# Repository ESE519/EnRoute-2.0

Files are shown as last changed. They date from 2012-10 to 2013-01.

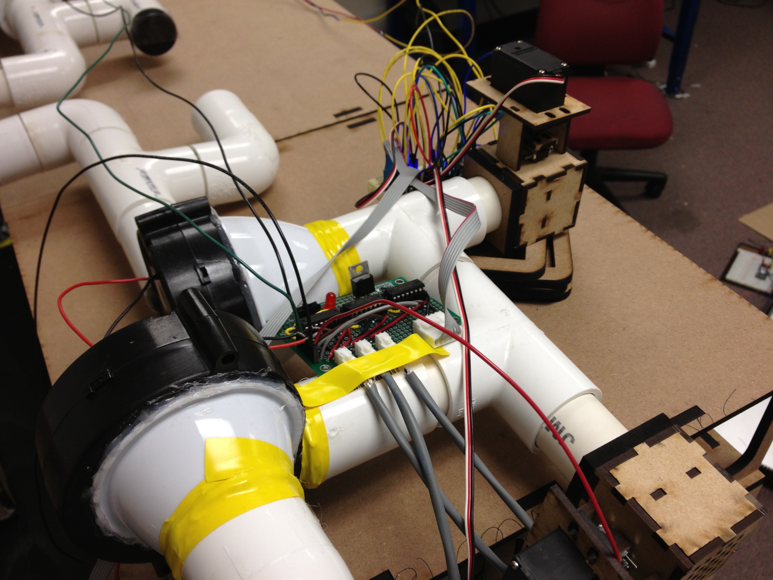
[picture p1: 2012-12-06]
PhotoShoot/Pics_11_30/Photo Nov 28, 2 21 02 PM.jpg

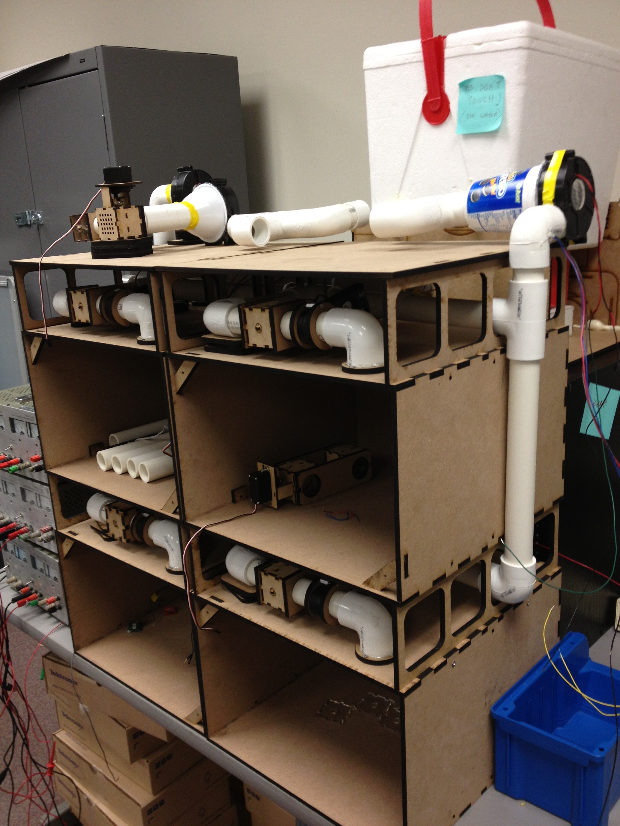
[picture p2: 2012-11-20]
PhotoShoot/Pics_11_19/Photo Nov 19, 3 16 37 PM.jpg

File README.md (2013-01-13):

EnRoute-2.0
===========

This is team 01's final project for Real Time and Embedded Systems course (ESE 519), fall 2012. 
The project is version 2.0 of EnRoute 1.0, an intelligent HVAC testbed.

Team Members:
1) Shah, Neel S.      : shahneel@seas.upenn.edu
2) Vadakedathu, Larry : vlarry@seas.upenn.edu
3) Wheeler, Dan       : dwheeler@seas.upenn.edu

Thank you!

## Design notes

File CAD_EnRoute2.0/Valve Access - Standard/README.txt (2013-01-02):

Valve Access:
These small pieces forms the link with the servo with the help of a 2*4-40 1/2" bolts and corresponding nuts & washers.
This is applicable to any type of valve in this testbed.

EnRoute2.0

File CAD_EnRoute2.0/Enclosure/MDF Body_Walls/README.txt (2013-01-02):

1) Due to the sheer dimensions of the walls, they were not laser cut but measured and cut using a power saw. 
2) The design is such that the front cover can be completely taken out but unscrewing from the L-brackets.
3) These L-brackets are screwed in with our custom designed nut-lock.

EnRoute2.0

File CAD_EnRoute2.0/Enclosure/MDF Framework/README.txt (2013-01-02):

Enclosure Front:
1) In red, the MDF pieces that form the framework including the handles and connecting pieces.
2) In white, how the complete front looks. The center window is 2*(32X16) clear acrylic sheets.

EnRoute2.0

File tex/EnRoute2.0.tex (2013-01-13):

\documentclass[a4paper,10pt,twocolumn]{article}
\usepackage{fullpage}
\usepackage{hyperref}
\usepackage{epsfig}
\usepackage{graphicx}
\usepackage{caption}
\usepackage{subcaption}

\usepackage{stfloats}

\begin{document}

\title{{\bf EnRoute 2.0 - The HVAC Test-Bed} \\ \normalsize\url{https://github.com/ESE519/EnRoute-2.0/wiki/_pages}}
\date{December 15, 2012}
\author{Dan Wheeler \\dwheeler@seas.upenn.edu
        \and Larry Vadakedathu \\vlarry@seas.upenn.edu
	\and Neel D Shah \\shahneel@seas.upenn.edu}
\maketitle

\begin{figure}[ht]
\centering
\epsfig{file=enroute2.eps,width=\linewidth,clip=}
\caption{EnRoute2.0 Complete Assembly}
\label{enroute2}
\end{figure}

\vspace{-5 mm}

\begin{center}
{\bf Introduction}
\end{center}

EnRoute 2.0, as seen in \ref{enroute2}, is an expansion project based on previous work--EnRoute:  The Energy Router Test-Bed--which was aimed at creating a building simulation test-bed for the testing of control algorithms with the goal of improvements in energy scheduling and peak power reduction.  EnRoute 2.0 hopes to expand on the original project through two major components:  creating a more realistic test-bed more closely related to real world HVAC systems, and allowing anyone to run simulations on the test-bed remotely.  The first task is achieved largely through the introduction of ductwork with Variable Air Volume (VAV) control to each room handled through small servo valves and an Air Handling Unit (AHU) distributing air, reclaiming air, and recycling air.  Remote operation is achieved with IP communication using a static IP address supplied specifically for the master mBed controller of the system.

For large scale buildings, electricity costs vary with time based on total demand of the aggregate of consumers.  In such a scenario, energy can cost up to 200 times as much during peak operating hours as it does during normal operating conditions, or during the night when energy is at its cheapest due to low overall demand.  Additionally, peaks in power consumption of an individual facility can result in costly fines.  Therefore, if you can schedule your energy use efficiently to (1) avoid peaks in individual power, and (2) minimize the total power consumption during peak operating hours you could significantly reduce the total cost of electricity incurred.

Unfortunately, current systems are not designed to provide this type of operation.  Firstly, control units have no knowledge of how electricity costs are changing with time, and secondly, units operate almost entirely independent of each other.  We can view the second scenario in the case of cooling two rooms.  Initially one room is cooling while the other room is within its bounds for temperature control, therefore the system is only using approximately half its total power.  If the second room reaches its high threshold point it will switch on and both rooms will begin to cool.  If systems had an overall notion of what other nodes were doing it would be able to schedule the energy use so that all rooms stay within specified bounds, but also ensure that the system is not operating at maximum power if it does not need to be.

\begin{center}
{\bf Project Goals}
\end{center}

The first EnRoute project utilized four (4) mutually exclusive zones which were heated using incandescent lightbulbs with operation points at 0\%, 25\%, 50\%, 75\%, and 100\% of total power.  Cooling was not successfully implemented here, rather it was simulated by heating up the rooms and 'cooling' them by exhausting the warm air to the outside.  While algorithms were effectively developed on this system it lacked reality when compared to real-world buildings which most often achieve heating and cooling through HVAC units which deliver temperature controlled air from the unit itself to multiple rooms.  To improve the realistic aspects of this project we set out to design a system which mimicked an actual HVAC system as best we could as well as to provide methods for cooling.

\begin{figure}[t]
\centering
\epsfig{file=front.eps,width=0.8\linewidth,clip=}
\caption{View of All Zones}
\label{front}
\end{figure}

Firstly, an understanding of HVAC systems is critical to grasp what we wanted to achieve with this test-bed.  At the heart of every HVAC system is the Air Handler Unit (AHU) which has three main functions:  supply air to the ductwork using a blower, pull air from the rooms using a second blower, and allow for the ability to recycle air back into the HVAC.  Next most important are the cooling and heating coils, which are frequently (depending on the size of the system) located coaxially in the HVAC unit so that air is pulled over both coils in series.  A third important feature, which becomes critical for peak energy reduction, is the Variable Air Volume (VAV) control of the system which changes the amount of air pumped into the ductwork based on how much flow each room is requesting.  Our design seeks to meet all three of the goals with the implementation of an AHU, both heating and cooling elements, and VAV control.

The next goal of this project was aimed not only at creating a test-bed, but an open-source test-bed which could be used by anyone (assuming permission is given) to run their own simulations remotely (i.e. from anywhere in the world).  

\begin{center}
{\bf Hardware:  Structural Design and Implementation}
\end{center}

\emph{Zone Design:}
Building off of the general architecture of the original EnRoute model, we decided to proceed with the four room, two floor building model seen in \ref{front}.  We will refer to these floors as ‘zones’ in this project.  All four rooms were built with the same dimensions of 14.5" by 14.5" by 9.5" for better analysis of control algorithms.  These zones were completely laser cut out of quarter-inch medium density fiberboard (MDF) and held together by press fitting the edges.  The two zones are spaced four inches apart using a custom built bridge that aids the passage of necessary ductwork to and from each room.  In addition to this, we built completely detachable doors of 13.98" by 8.98" for the rooms which were also press fit to have minimal leakage from the rooms.

\emph{Duct Work:}
Four inches above the top zone we have the HVAC unit consisting of independent heating and cooling mechanisms, as well as separate duct work for recycle air and supply air.  The ductwork layout may be seen here \ref{ductwork}.  EnRoute 2.0 overall uses nearly 15 feet of PVC piping.  For each of the rooms, we have an inlet pipe through a valve and air flow meter, shown here \ref{vav}.  The supply air begins at the right top corner of the test bed in a series to parallel piping system that flows through each zone to the corresponding rooms.  In a similar layout, the outlet from each of the rooms is carried out in a parallel to series fashion to the HVAC unit where this recycled air is mixed with air from outside and fed back to the system.

\begin{figure}[t]
\centering
\epsfig{file=ductwork.eps,width=0.8\linewidth,clip=}
\caption{Ductwork Overview}
\label{ductwork}
\end{figure}

\begin{figure}[t]
\centering
\epsfig{file=vav.eps,width=0.8\linewidth,clip=}
\caption{VAV Control with Servo Valve}
\label{vav}
\end{figure}

\emph{Valve Design:}
The use of valves has significant effects on the working of our system.  They not only determine how much air needs to be passed into each room but also enable us to script advanced lazy  schedulers to minimize peak energy consumption by the system as a whole.  The valves were also laser cut and press fit with a combination of quarter-inch and eighth-inch MDF. We also put in a stopper to prevent any leakage when the valve is closed.  We make use of position servo-controlled custom built valves for this HVAC modelling system. There is one valve per room at the inlet and one each at the HVAC outlets. Since cooling and heating are the main tasks of any HVAC system, we designed a single-servo controlled double valve kept at a 90 degree offset to each other which ensured that our system was either cooling or heating at any given time.

\emph{Heating:}
We made use of a 12V hair dryer, shown in \ref{heater}, as our heating element for this test-bed. The output from one point of the double valve behaves as the input to the hair dryer which uses this air to blow over the heating coils and transfer heat to our system. This heated air is sucked in by our supply blower and sent in to the two zones and hence four rooms based on the temperature levels at the HVAC unit. Through experimentation, we realized that the heater would keep rising beyond 65 degree celsius. This is a potential safety concern and hence we limited this range in code to stay within 37 and 40 degree celsius.

\begin{figure}[t]
\centering
\epsfig{file=heater.eps,width=0.8\linewidth,clip=}
\caption{Heater}
\label{heater}
\end{figure}

\begin{figure}[b]
\centering
\epsfig{file=cooler.eps,width=0.8\linewidth,clip=}
\caption{Cooling Box with Copper Coil}
\label{cooler}
\end{figure}

\emph{Cooling:}
One of the main goals of designing such a scaled down version of an actual building with desired variable temperature is the cooling system. While hacking a refrigerator to make use of the compressor and related cooling elements would yield a much larger temperature difference, we decided to use a more conventional approach with a ‘bucket-of-ice’ seen in \ref{cooler}. In essence, we used a 13.5" by 11" by 11" styrofoam box with a 2 foot long half-inch diameter copper tube submerged in cubes of ice. With the other output point of the double valve open, we could circulate cool air in to the rooms using the same supply blower. We saw temperature drops of 5 to 6 degree celsius. This drop in temperature is very realistic but in order to monitor faster dynamics, we decided to build an enclosure for the entire system, excluding the cooling box.

\emph{Enclosure:}
Due to the large size and various number of linkages in the entire system, there would still be some leakage and this would affect the dynamics of the system in a very slow and realistic manner. But since this is meant to be a test bed we need to be able to implement algorithms and see the results as soon as possible. This is the primary purpose of the enclosure, which can be seen in \ref{encl}, to help accelerate our simulations on EnRoute 2.0. The enclosure measures 38.5" by 42.5" by 20" and is designed for minimum raw material requirements. This means that we made a frame out of MDF and the view window out of two 16" by 32" clear acrylic sheets. To simulate natural heating in a building due to the sun, we decided to use an incandescent bulb. Since the dimensions of the enclosure exceed the workspace limits of the laser, we cut and built the enclosure using conventional power tools.

\begin{figure}[t]
\centering
\epsfig{file=encl.eps,width=0.8\linewidth,clip=}
\caption{Enclosure Design}
\label{encl}
\end{figure}

\begin{center}
{\bf Electronics}
\end{center}

As mentioned earlier, valves in every room are controlled by small servo motors. These servo motors, shown in \ref{servo}, are position servo motors controlled using the PWM pins on the mBed. Each valve is controlled separately by a servo motor.  The servo motor that we used can be found here (https://www.sparkfun.com/products/9064).    

The temperature sensors \ref{temp} that we use are TMP-36. This sensor is inexpensive and provides an analog voltage based on the ambient temperature and so were connected to the mBed using ADC input pins. This sensor can be found from (https://www.sparkfun.com/products/10988?).  We placed one temperature sensor in each zone, one outside the zones but inside the enclosure, and one in the supply air duct 

We use a total of 3 blowers, as shown here \ref{blower}, to force air through the ductwork.  These blowers can be found at (https://www.sparkfun.com/products/11270).  This blower provides in excess of 12 CFM of flow at 1A of rated current, which worked well for us.  The forward blower pulls air from the heater or cooler and delivers it to the ductwork. The return blower is used to suck the air out from each zone and the third valve was used to pass air from the return valve to either the heater or cooler.

\begin{figure}[t] 
	\centering
        \begin{subfigure}[l]{0.4\columnwidth}
		\centering
		\epsfig{file=blower.eps,width=1\linewidth,clip=}
		\caption{Blower}
		\label{blower}
        \end{subfigure}
        \begin{subfigure}[r]{0.4\columnwidth}
		\centering
		\epsfig{file=temp.eps,width=\linewidth,clip=}
		\caption{Temp Sensor}
		\label{temp}
        \end{subfigure}
	\\
        \begin{subfigure}[r]{0.4\columnwidth}
		\centering
		\epsfig{file=servo.eps,width=0.8\linewidth,clip=}
		\caption{Servo}
		\label{servo}
        \end{subfigure}
	\caption{Electronics}
        \label{electronics}
	\vspace{-7mm}
\end{figure}

\begin{figure}[b!]
\centering
\epsfig{file=flow.eps,width=0.3\linewidth,height=0.7\linewidth,clip=}
\caption{Flow Meter}
\label{flow}
\end{figure}

These blowers need a 12V supply, so we use the SN754410 H-Bridge to produce a 12V signal from a 5V PWM input signal supplied from the mBed.  These H-Bridge circuits are rated for up to 1A continual current draw which is the maximum our blowers are rated for.

We use air flow meters, displayed here \ref{flow}, from Ambient Weather (http://www.ambientweather.com/amhp816a.html) to measure the speed at which air is entering the zones as well as the airflow near the forward valves. Speed data is then converted to volumetric flow rate in CFM (cubic feet per minute) for displaying in the GUI.

\begin{center}
{\bf Software}
\end{center}

Software for this project is implemented both on mBed microcontrollers, which are the nodes physically interfaced with the test-bed, and in MATLAB, which acts as the master planner of the system by gathering all data and calculating the control outputs for the servo valves and blower states.  The system architecture for our system can be seen here \ref{sys_arch}.

\begin{figure}[b!]
\centering
\epsfig{file=sys_arch.eps,width=\linewidth,clip=}
\caption{System Architecture}
\label{sys_arch}
\end{figure}

The system utilizes three mBeds:  one for the lower zone that controls rooms 3 and 4, one for the upper zone that controls rooms 1 and 2, and one for the HVAC and AHU system.  The mBeds placed in each zone gather and interpret data from temperature sensors and flow meters, relay this data to the HVAC mBed over RS232 protocol, and subsequently receive control data from the HVAC mBed which defines how the servo position should be set.  The HVAC mBed also reads from two temperature sensors and a single flow meter, then requests and receives data from the two zone mBeds subsequently, and transmits all data to the host PC.  Additionally, data returned from the PC instructs the HVAC mBed how to control the recycle air valves and AHU blowers.

Within MATLAB a front-end GUI has been created which allows the user to view all data from the test-bed, in real time while the simulation is running, and control all controllable devices (servo valves, heating or cooling, and blowers).  The Overview tab, shown here in \ref{overview_tab}, displays all data from the four rooms and provides a means for manual control over the servo valve for each zone.  Additionally, there are tabs which display all data simultaneously for each room.  The HVAC tab, shown in \ref{HVAC_tab}, allows control of the recycle air valves and blower states.  Also, data is plotted for all HVAC devices including a current sensor monitoring the supply blower.  Finally, the Control tab provides the user a way to control all aspects of the system including room set points, control algorithms, serial port, IP address (see below), whether the system is heating or cooling, and several other features.  This tab is shown in \ref{control_tab}.  

\begin{figure*}[t]
\centering
\epsfig{file=overview_tab.eps,width=\linewidth,clip=}
\caption{Dashboard Overview Tab}
\label{overview_tab}
\end{figure*}

\begin{figure*}[b!]
\centering
\epsfig{file=HVAC_tab.eps,width=\linewidth,clip=}
\caption{Dashboard HVAC Tab}
\label{HVAC_tab}
\end{figure*}

\begin{figure*}[t]
\centering
\epsfig{file=control_tab.eps,width=\linewidth,clip=}
\caption{Dashboard Control Tab}
\label{control_tab}
\end{figure*}

In order to have the test-bed be controlled from virtually anywhere in the world we decided to incorporate IP-IP communication. The mBed inherently supports Ethernet, so we realized a UDP server on the mBed and our MATLAB GUI acted as the UDP client. The client (MATLAB) sends a packet to the server (mBed) requesting data. The mBed then parses the packet which contains instructions as per the user’s input. The mBed, at the same time, also collects data such as the temperature, flow rate, and servo motor position, passing it back to the client as a UDP packet.

\begin{figure}[t]
\centering
\epsfig{file=blower_mdl.eps,width=\linewidth,clip=}
\caption{Blower Control Model}
\label{blower_mdl}
\vspace{-5mm}
\end{figure}

Additionally, since not all those interested in testing algorithms are intimately familiar with MATLAB programming, the system will accept control algorithms designed in MATLAB as long as they follow a basic template design.  For example, the blower control model MUST have eight total inputs (four for valve position and four for flow meters, in this order) and a single output which defines the percent of max power supplied to the blower.  An example model may be seen in \ref{blower_mdl}.  If the user wishes to define more inputs (in the form of constants), a single initialization file can be edited to load the inputs at the beginning of the control loop.  This is best done for inputs that do not change (such as set points).  An example of such a case can be seen in \ref{lazy}, which has constant inputs for set points and control limits for the lazy scheduler.

\begin{figure}\centering
        \begin{subfigure}[t]{\linewidth}
                \centering
                
                \caption{Lazy Scheduler Model}
                \label{lazy_mdl}
        \end{subfigure}
	\\
        \begin{subfigure}[b]{\linewidth}
                \centering
                
                \caption{Code Sample for Model Initializer}
                \label{lazy_code}
        \end{subfigure}
        \caption{More Advanced Model w/ Constant Inputs}\label{lazy}
\end{figure}

\begin{center}
{\bf Use as a Test-Bed}
\end{center}

With our custom designed front-end system in MATLAB interfaced with our main mBed controller, we control the working of the test bed. The control could be manual from the user or from a Simulink model fed in by the user. This is one of the key advantages of our test bed where a user with minimal experience can put in a simple simulink model and let our system simulate the results.

As mentioned earlier, the AHU is the main component of any HVAC system. We used 3 blowers for this purpose. When we triggered the supply blower, based on the mode (cooling or heating) selected, the room temperatures would vary accordingly. Further temperature variations were seen based on the angle of the corresponding room valves that were also controlled from our GUI. These valve angles were determined based on the temperature requirements of the room under question. It is imperative for an energy efficient system to adjust the amount of air pumped in based on the requirements of the room i.e if a valve to a room is closed, it doesn’t make sense in supplying the same amount of air for the other 3 rooms especially if those rooms don’t need it. This is where the lazy scheduler plays a big role in determining efficient energy utilization throughout the entire piping.  

A very useful feature we incorporated into this revision of EnRoute is the ability to remotely do all of the above and not be tethered to the system during operation.  We achieved this over the internet using dedicated IPs for viewing and controlling the system.

\begin{center}
{\bf Simulation Results}
\end{center}

The simplest algorithm for testing is a pure ON-OFF controller that will keep all zones oscillating between their high and low set points with no regard to total simultaneous power consumption.  Using this type of test we can confirm that the systems are functioning as they should as well as gain an understanding of the dynamics for the rooms.  These simulations were run using the heating aspect of the system which requires control of the outlet air temperature.  If the heater were left unconstrained it would quickly become too hot and would damage the system; therefore, the mBed limits the heater output temperature to within a small acceptable range.  Using this heater output we have implemented an ON-OFF controller whose simulation results for Room 1 are shown in \ref{on_off_rm1_temp} and the total blower power during the simulation is shown in \ref{on_off_blower}.  It is worth noting that the blower is constrained to operate in the 60\% to 100\% range.

\begin{figure}[t]
\centering
\epsfig{file=on_off_rm1_temp.eps,width=\linewidth,clip=}
\caption{Room 1 Temperature Response to On-Off Control}
\label{on_off_rm1_temp}
\end{figure}

\begin{figure}[t]
\centering
\epsfig{file=on_off_blower.eps,width=\linewidth,clip=}
\caption{Room 1 Temperature Response to On-Off Control}
\label{on_off_blower}
\end{figure}

\begin{figure}[b!]
	\centering
        \begin{subfigure}[t]{\linewidth}
                \centering
                
                \caption{Lazy Scheduler Blower Output}
                \label{k_lazy_blower}
        \end{subfigure}
	\\
        \begin{subfigure}[b]{\linewidth}
                \centering
                
                \caption{Room 1 Temperature Response Lazy Scheduler}
                \label{k_lazy_rm1_temp}
        \end{subfigure}
	\\
        \begin{subfigure}[b]{\linewidth}
                \centering
                
                \caption{Room 3 Temperature Response Lazy Scheduler}
                \label{k_lazy_rm3_temp}
        \end{subfigure}

        \caption{Lazy Scheduler Simulation}\label{lazy_sim}
\end{figure}

For further testing of our system we implemented a basic lazy scheduler algorithm.  A lazy scheduling algorithm only makes intelligent decisions when a room reaches a threshold point by either closing the air flow to the room or setting the room as critical.  Simulation results for this test are shown in \ref{lazy_sim} and \ref{lazy_sim_valve}.

\begin{figure}[t]
	\centering
        \begin{subfigure}[b]{\linewidth}
                \centering
                
                \caption{Room 1 Valve Response Lazy Scheduler}
                \label{k_lazy_rm1_valve}
        \end{subfigure}
	\\
        \begin{subfigure}[b]{\linewidth}
                \centering
                
                \caption{Room 3 Temperature Response Lazy Scheduler}
                \label{k_lazy_rm3_valve}
        \end{subfigure}
        \caption{Lazy Scheduler Simulation}\label{lazy_sim_valve}
\end{figure}

The goal of this project was not to design sophisticated test algorithms for furthering research into energy scheduling, it was to design a test-bed so that others may develop algorithms and test them independently.  Therefore, little time was spent designing these controls and more time was focused on building a simple user interface which would allow others to easily load and test their own algorithms.

\begin{center}
{\bf Future Work}
\end{center}

Our list of proposed future work includes the following items:

1.  The ice box worked really well for us giving us a change of 5 deg C, but this change was not realized once the test-bed was assembled. We do realize that the dynamics of the system can be greatly improved if, instead of using a styrofoam box filled with ice as a cooling unit, we use a heat pump of some sort (i.e. the internal workings of a fridge) for the cooling mechanism.  

2.  Currently we have a common heating system for all the zones which makes it difficult for the user to keep test individual dynamics of each zone. We will want to incorporate the ability to control heat into each room individually through the use of some type of local reheat element. This would make our current system more flexible.

3.  Increasing the airflow to each room would improve dynamics and reduce the time to heat and cool each zone.  To achieve this small CPU fans could be added to the inlet of each room.  This requires little hardware work, but will involve more significant software and electronics modifications if the fans should be controllable.

4.  All systems used in real buildings implement a protocol called BACnet to interact with each other. So to take this system one step further towards a realistic system we will want to create a BACnet server on the mBed. In our endeavor to take this system further towards reality we wish to replace our mBeds with real BACnet clients and BACNet servers.

5.  Currently we have tested a bare minimum lazy scheduler as well as a more advanced lazy scheduler. Other algorithms/scheduling policies are something that will be implemented.

\vspace{5mm}

\begin{center}
{\bf Conclusion}
\end{center}

In this project we set out to design a test-bed for remote investigation of control algorithms aimed at green scheduling practices.  With high costs of electricity during peak operating hours, significant savings can be realized through effective control structures designed at limiting the total simultaneous power consumption through a system integration approach.  Our design includes an air handling unit, variable air volume control, ductwork, heating, and cooling elements to more accurately portray commercial buildings than previous models.  The user interface is designed such that control algorithms may be designed in Simulink and loaded into the system for those unfamiliar with programming, as well as allowing for communication to the host system through IP so that the test-bed can be controlled remotely from any computer with an internet connection.  Future research will be conducted using this test-bed as a base for control model testing and analysis, which may provide more accurate results than using purely simulated results while at a reduced cost and level of complexity of testing in actual buildings.

\end{document}

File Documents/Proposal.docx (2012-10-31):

EnRoute Proposal

Abstract

The EnRoute project will focus on designing a building model with a scaled down HVAC unit and implementing controls on mbeds that communicate to Matlab via BACnet. The HVAC unit will handle heating and cooling, as well as airflow through the ductwork using one blower (https://www.sparkfun.com/products/11270) for supply and one for return air. Return air can be recycled to the HVAC or vented to the outside. Control for this project will use three mbeds. There will be one mbed per story, and one master controller for the HVAC. The mbeds for each story will take measurements, control the valves, and control the heating bulb. The master mbed will control the HVAC unit and handle communication to the host computer. We will also incorporate a flow sensor in and add sensors for measuring power consumption.

Work Completed

The Phase 1 work is listed here:

1. Prototype Design for a single room

2. Begin electrical network over serial

3. Prototype damper valves

4. Test Heating/Cooling methods

(1) We have designed & built a single room (14”x14”x9”) using ¼ MDF. The design is such that the ceiling can be placed and removed easily when we want to acquire data. Each of the inner edges have been made air-tight using spray foam, and the outer edges where necessary with hot glue. All the connections in our prototype make use of 1” PVC pipe. The inlet blower is connected (via 1” PVC pipes) to the inlet point of the room situated at one ceiling corner of the room with the Peltier enclosure and control valve in between. To channel the air being sucked out of the room, we utilized available items to construct the necessary attachment to the blower.

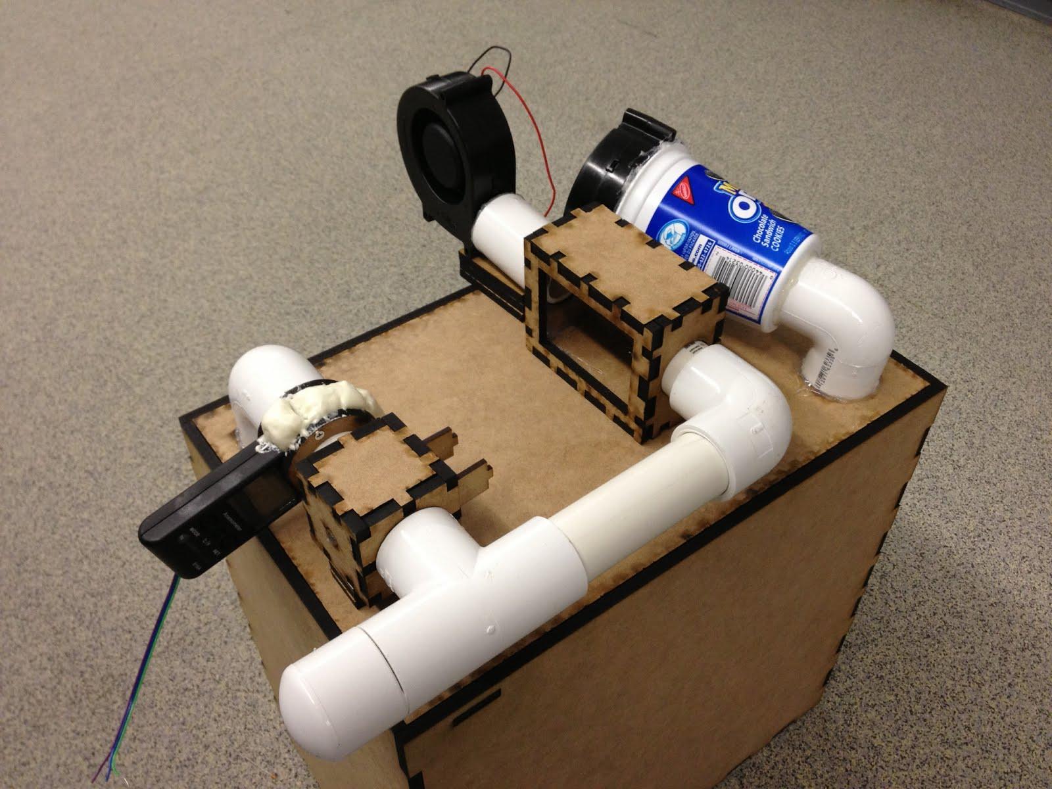
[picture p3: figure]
A description...

(2) We have individually tested each and every component like the blower, Peltier effect sensor/actuator, airflow sensor etc. by interfacing it with the mBed. Our blower’s maximum speed can be read with the Airflow sensor so we are not looking for a professional air flow sensor. Now we have to integrate them all to evaluate real-time performance. We hooked up the temperature sensor (SHT-15) to the mBed and placed this setting inside our room to monitor temperature variability. The test results have been discussed in section 4) of this write-up.

(3) We built a MDF based control valve with special consideration for motor shaft connectivity to the valve and rotary constraints of the valve itself. Once again insulation as mentioned earlier was checked. Also,using MDF we built a setup for the airflow sensor to be able to connect to the 1” pipes. With the valve completely open, we measured close to 9m/s flow velocity and about 1m/s with the valve closed.

(4) We built a simple MDF based encasing for the peltier sensor, placed a heat sink on one side with thermoelectric tape in between them to test the functionality of the sensor for our purposes. After hours of testing, we noticed that we got a temperature variance of +/- 2 deg celcius only. This seemed to have improved a bit after placing a small CPU fan at the heat sink in the hope of cooling the other side faster to lower temperatures. However, the variacne remained nearly the same. We have been thinking of using multiple peltier sensors together to study the effect but not yet implemented. We used an H-bridge to change the hot & cool sides of the sensor.

Unfortunately from the tests and research later, we may have come to the realization that while these tiny peltier sensors are excellent at providing large changes in temperature, they are stubborn in transferring these changes.

Plan Forward

Currently we are on schedule with a single room prototype, although the Peltier unit did not work to our liking. We are moving forward implementing a resistive heating coil for heating, and will explore cooling later on as time permits. Our attention will now shift to constructing the entire structure with four heating/cooling zones, running the duct work, designing the HVAC, creating a MATLAB interface, and controlling the structure with BACnet. Phase 2 and 3 are laid our as follows:

Phase 2: To be completed by November 16th

Finalize building design and construction. (Dan/Larry)

Implement controls in building. (Dan/Larry/Neel)

Begin work on BACnet communication. (Neel)

Phase 3: To be completed by November 27th

Modify building to fit last minute additions. (Dan/Larry)

Implement MATLAB and GUI control. (Dan/Larry)

Finalize BACnet communication. (Dan/Larry/Neel)

Add building enclosure. (Dan/Larry)

EnRoute 2.0 Neel Shah, Larry Vadakedathu, Dan Wheeler Date:10/29/2012

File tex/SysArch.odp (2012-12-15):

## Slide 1

MATLAB

(Master Control)

Wireless Communication link

mbed MicroController

HVAC Unit

Serial Communication Link

mbed MicroController

Zone 1

Serial Communication Link

mbed MicroController

Zone 2

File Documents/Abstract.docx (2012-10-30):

EnRoute Abstract

The EnRoute project will focus on designing a building model with scaled down HVAC unit and implementing controls on mbeds that communicate to Matlab via BACnet. Our building will consist of four heating/cooling zones with two levels featuring adjoining rooms. The HVAC unit will be on the roof of this building and circulate air using 1” PVC pipe. Supply entry points are restricted using a servo control valve.

The HVAC unit will handle heating and cooling, as well as airflow through the ductwork using one blower (https://www.sparkfun.com/products/11270) for supply and one for return air. Return air can be recycled to the HVAC or vented to the outside. Fresh air can also be pulled into the HVAC. Heating and cooling will be handled with a peltier thermoelectric cooler or a resistive electric heater and chilled water.

Control for this project will use three mbeds. There will be one mbed per story, and one master controller for the HVAC. The mbeds for each story will take measurements, control the valves, and control the heating bulb. These mbeds will communicate over RS232 to the master. The master mbed will control the HVAC unit and handle communication to the host computer. We will also incorporate a flow sensor in and add sensors for measuring power consumption.

Phase 1: To be complete by November 2nd

- Prototype design for single room. (Dan/Larry)
  - Test blowers to ensure they are powerful enough.
- Begin electrical network over serial. (Neel)
- Prototype damper valves and validate performance. (Dan/Larry)
- Test Peltier unit to ensure proper functionality. (Dan/Larry/Neel)
  - If this unit is not effective, test chilled water cooling.

Phase 2: To be completed by November 16th

- Finalize building design and construction. (Dan/Larry)
- Implement controls in building. (Dan/Larry/Neel)
- Begin work on BACnet communication. (Neel)

Phase 3: To be completed by November 27th

- Modify building to fit last minute additions. (Dan/Larry)
- Implement MATLAB and GUI control. (Dan/Neel)
- Finalize BACnet communication. (Dan/Larry/Neel)
- Add building enclosure. (Dan/Larry)

Extra-Credit Aspects:

- Local reheat units.

EnRoute 2.0 Neel Shah, Larry Vadakedathu, Dan Wheeler

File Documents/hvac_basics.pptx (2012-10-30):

## HVAC Basics

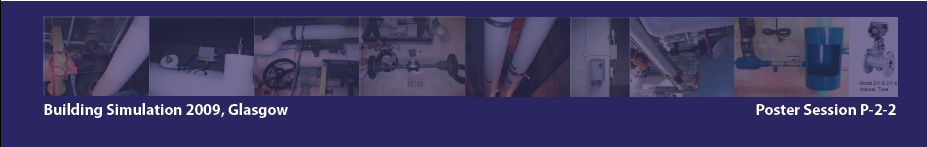
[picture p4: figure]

Bin Yan

HVAC – Heating, Ventilation, Air-conditioning

## HVAC Energy Consumption

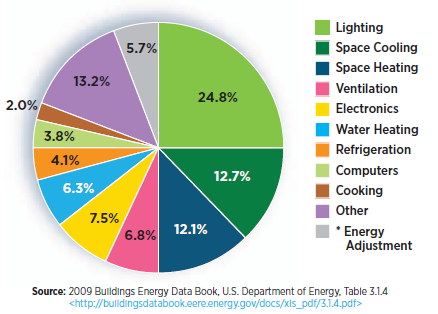
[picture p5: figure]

Annual Energy Use

Cooling 642 kWh/m²
Heating 623 kWh/m²
Electricity 414 kWh/m²

32%

>60%

DOE numbers

A lab building on campus

## HVAC

HVAC – Heating, Ventilation, Air-conditioning

Temperature

68°F (20°C) and 75°F (25°C)

Humidity

30% relative humidity (RH) and 60% RH

A slightly positive pressure to reduce outside air infiltration.

Pressure

Rooms typically have several complete air changes per hour

Ventilation

Diagram of mechanical system on the blackboard

## Where?

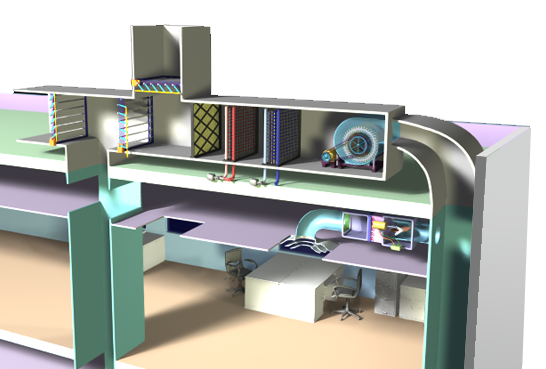
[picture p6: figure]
image of hvac on roof of building
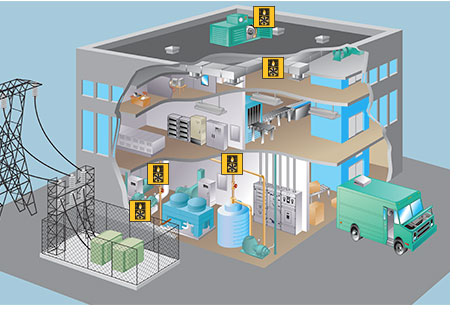
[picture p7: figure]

Mechanical Room: Boilers, chillers, pumps, heat exchangers…
Air Handling Units (AHUs): heat, cool, humidify, dehumidify, ventilate, filter and distribute the air.

Room Controls: thermostats and Variable Air Volume (VAV) boxes

Pictures from http://www.learnhvac.org/

## In the mechanical room

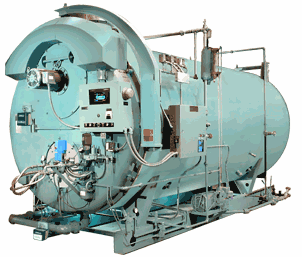
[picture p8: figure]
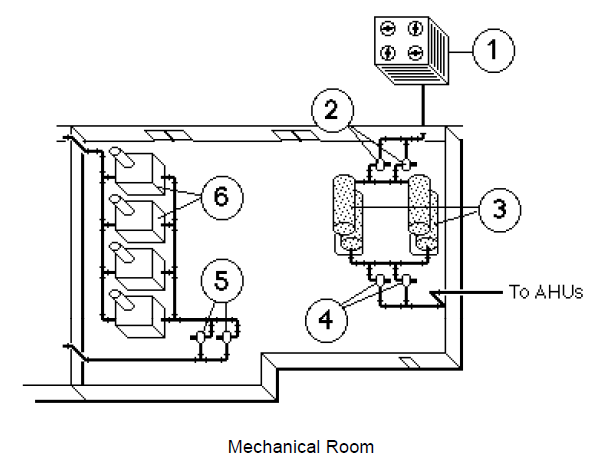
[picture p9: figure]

Boiler

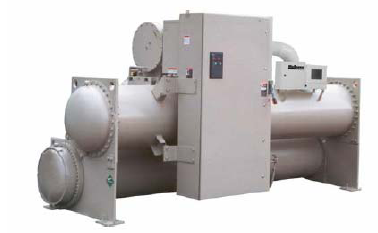
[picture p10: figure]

Chiller

Pictures from https://rfd-training.tac.com/docs/HVAC.pdf

## Heating

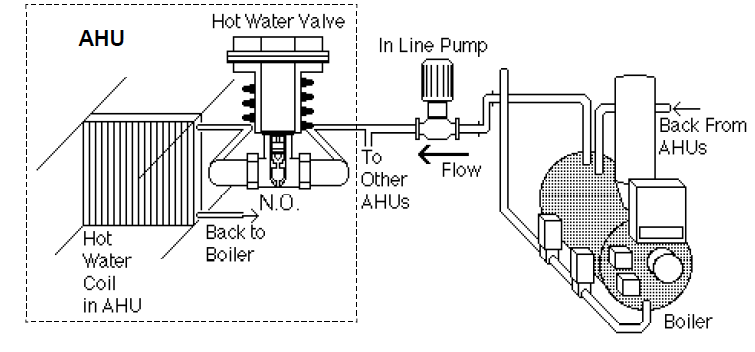
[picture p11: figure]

Also to radiators, terminal reheat, domestic hot water.

Pictures from https://rfd-training.tac.com/docs/HVAC.pdf

## Heating

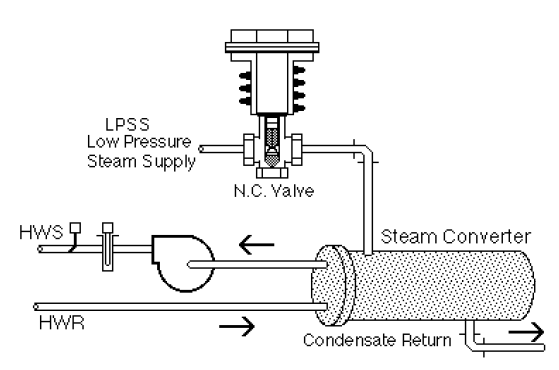
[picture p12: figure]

Pictures from https://rfd-training.tac.com/docs/HVAC.pdf

## Cooling

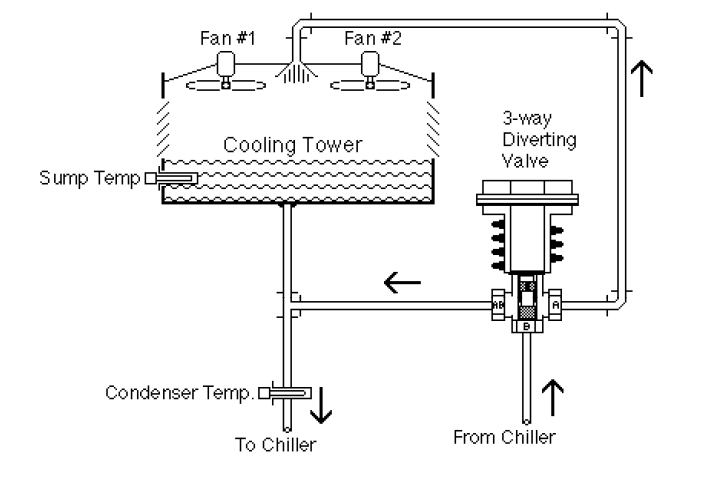
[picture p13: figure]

Pictures from https://rfd-training.tac.com/docs/HVAC.pdf

## AHU – Air Handling Unit

Where does air come from and go to?

Exhaust air

Return air

Outside air

Supply air

## AHU

What’s in an AHU?

Sensor

Heating/Cooling Coil

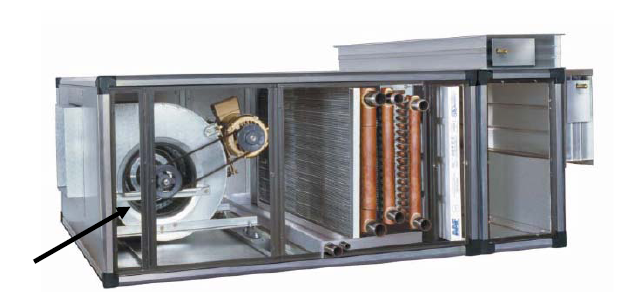
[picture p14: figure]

Pictures from https://rfd-training.tac.com/docs/HVAC.pdf

Damper

Filter

Fan

## AHU - Economizer

Linked

Minimum in summer
More outside air in winter

55°F

Economizer mode: Using outside air for cooling rather than mechanical cooling.

Pictures from https://rfd-training.tac.com/docs/HVAC.pdf

## AHU – Heating and Cooling

55°F

dehumidification

Pictures from https://rfd-training.tac.com/docs/HVAC.pdf

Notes: The AHU SAT = 55 all the time

## Humidification

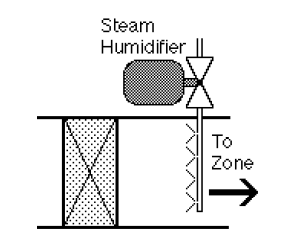
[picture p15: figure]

Why before the cooling coil?

Pictures from https://rfd-training.tac.com/docs/HVAC.pdf

## VAV

damper

Two variables – Temperature & Air Volume

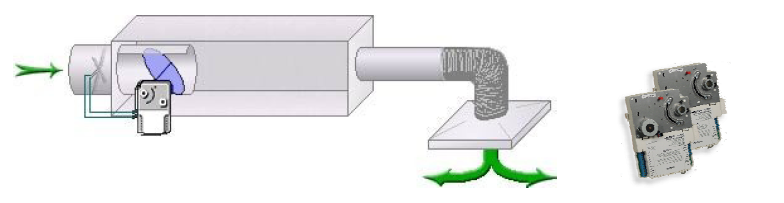
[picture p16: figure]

The box you can see in the hallway.

IF temperature too high

First reduce reheat till fully closed
Then increase air volume

IF temperature too low

First reduce air volume till minimum
Then start reheat

Pictures from https://rfd-training.tac.com/docs/HVAC.pdf

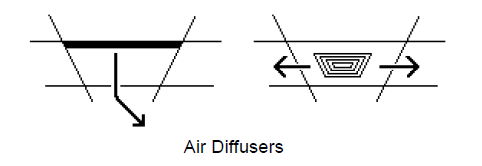
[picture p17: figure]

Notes: Add labels
If statement

## Winter

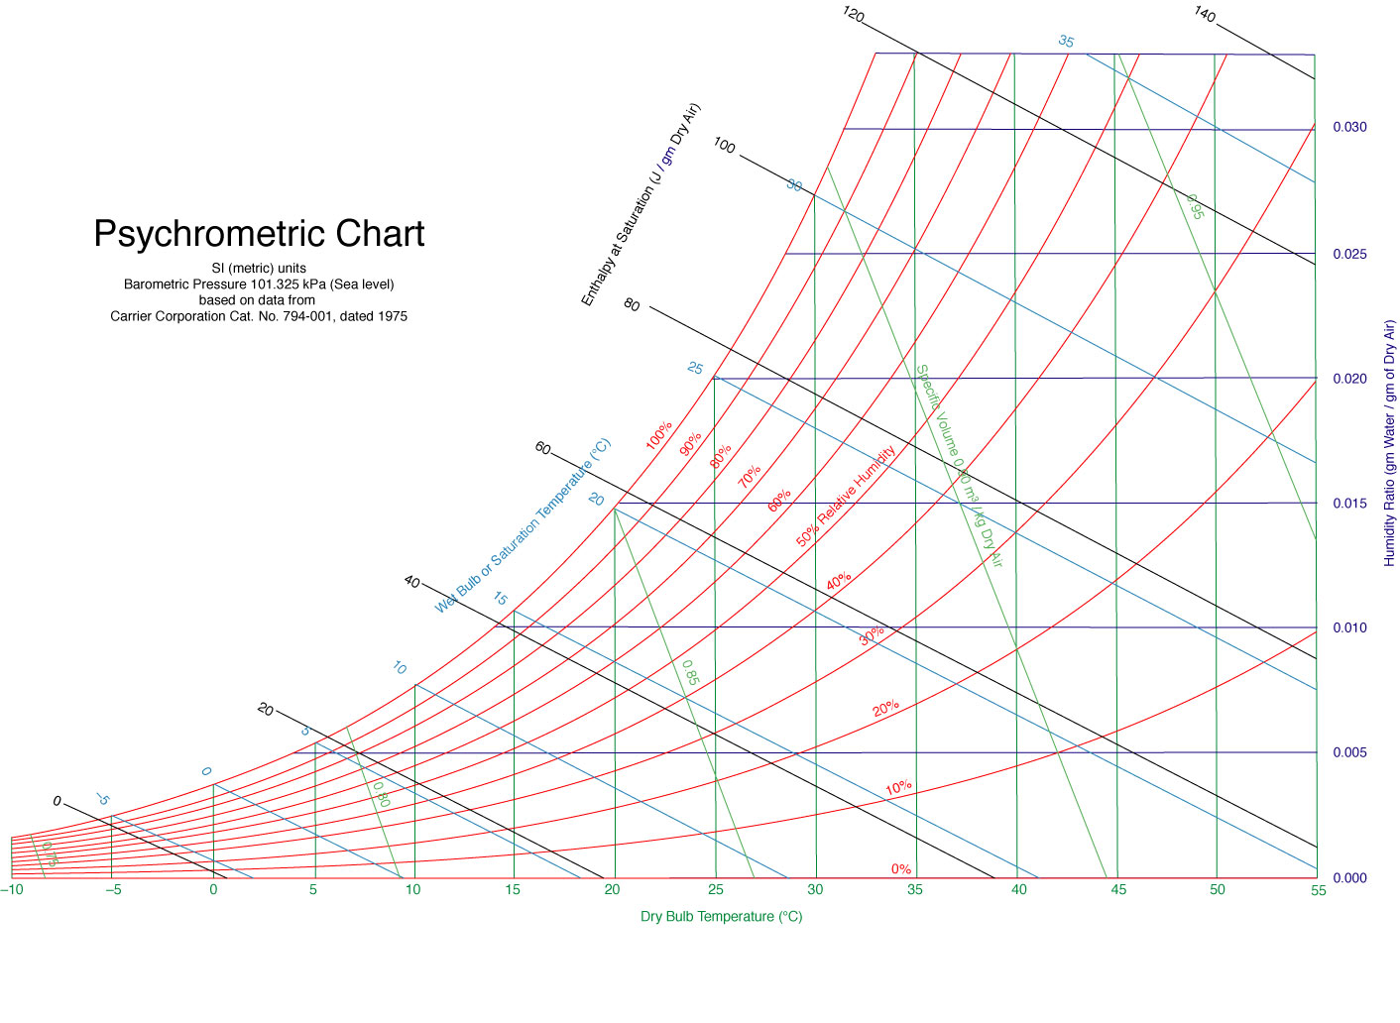
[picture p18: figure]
PsychrometricChart-SeaLevel-SI

Outside

Mixed

Return

## Summer

Outside

Cooled and dehumidified

Mixed

Return

## The Real World

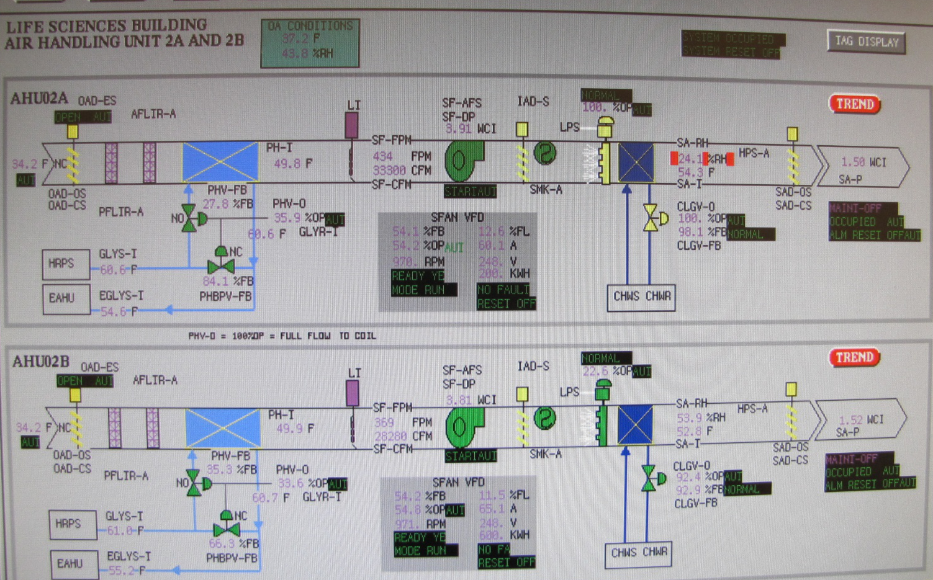
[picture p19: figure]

52°F

Any difference? Anything wrong?

## The Real World

Chilled water is still used when outside air is far below 52F

52°F

Temperature increased after humidification.
Sensor error.
Separate control caused counteraction.

## What we have learned?

The system that ensures the thermal comfort.

What’s in the mechanical rooms.

What happens in air handling unit.

How VAV works.

What can happen in the real world.

## Thanks!

binyan@design.upenn.edu

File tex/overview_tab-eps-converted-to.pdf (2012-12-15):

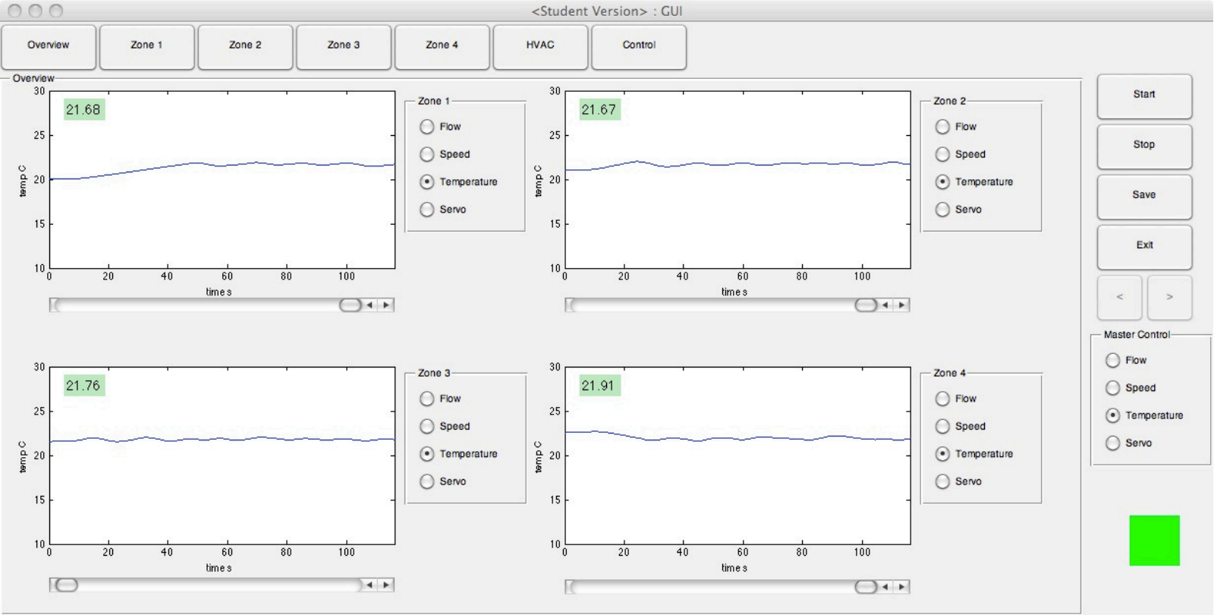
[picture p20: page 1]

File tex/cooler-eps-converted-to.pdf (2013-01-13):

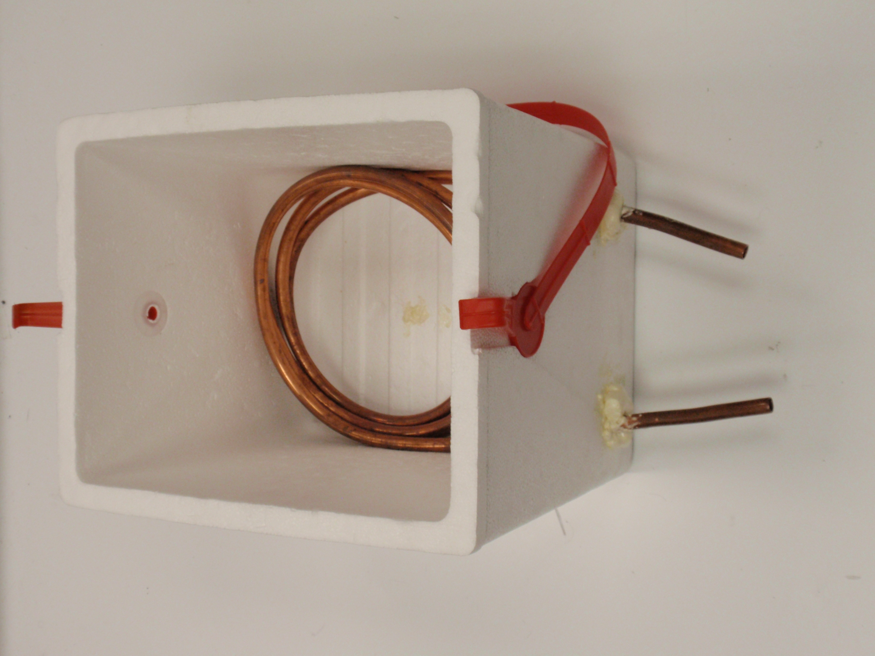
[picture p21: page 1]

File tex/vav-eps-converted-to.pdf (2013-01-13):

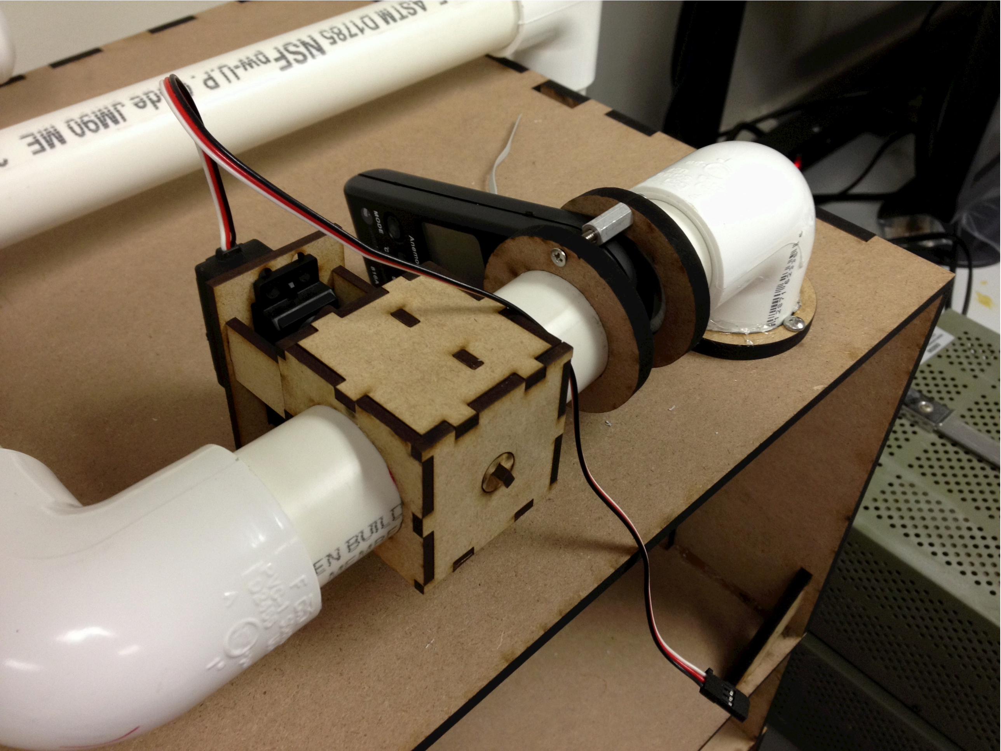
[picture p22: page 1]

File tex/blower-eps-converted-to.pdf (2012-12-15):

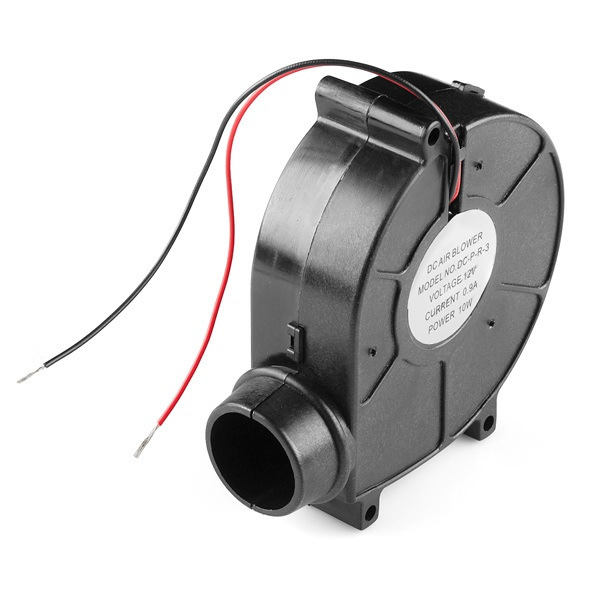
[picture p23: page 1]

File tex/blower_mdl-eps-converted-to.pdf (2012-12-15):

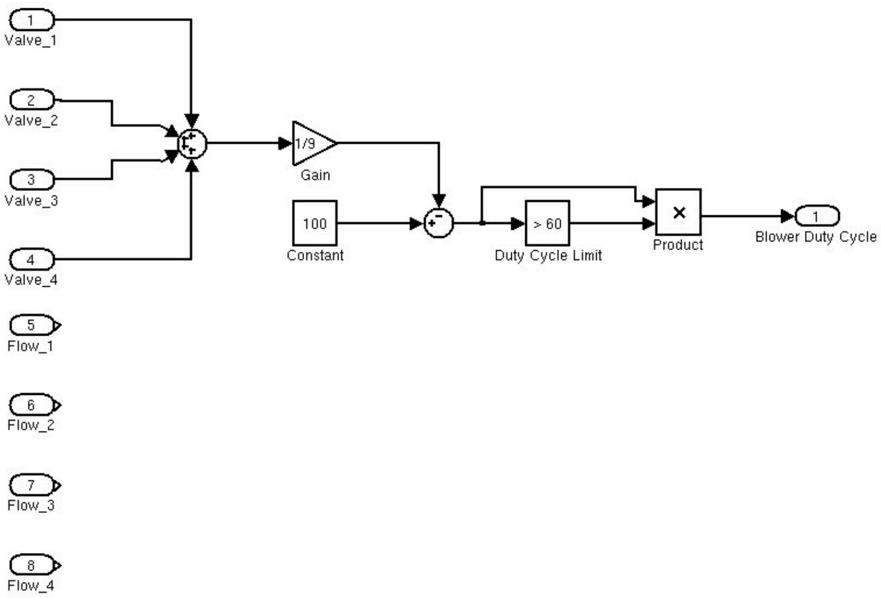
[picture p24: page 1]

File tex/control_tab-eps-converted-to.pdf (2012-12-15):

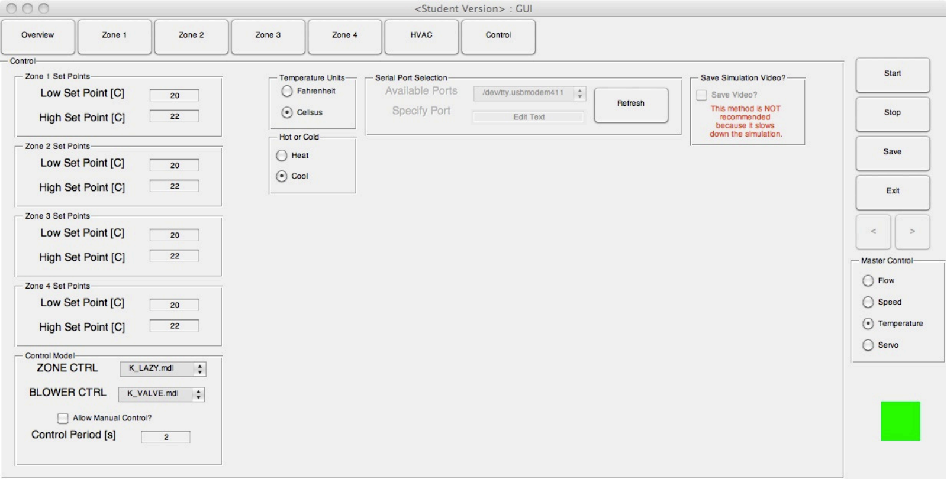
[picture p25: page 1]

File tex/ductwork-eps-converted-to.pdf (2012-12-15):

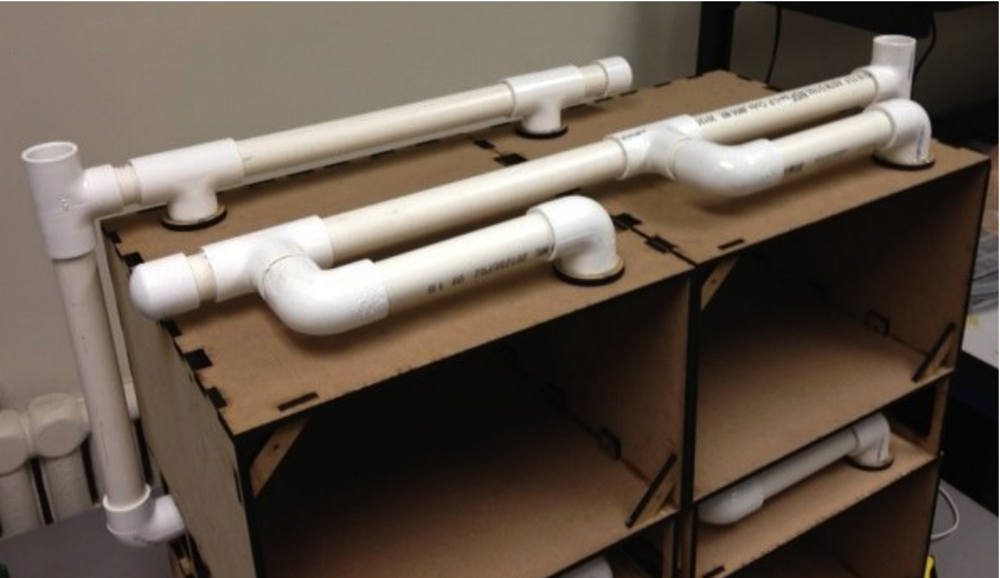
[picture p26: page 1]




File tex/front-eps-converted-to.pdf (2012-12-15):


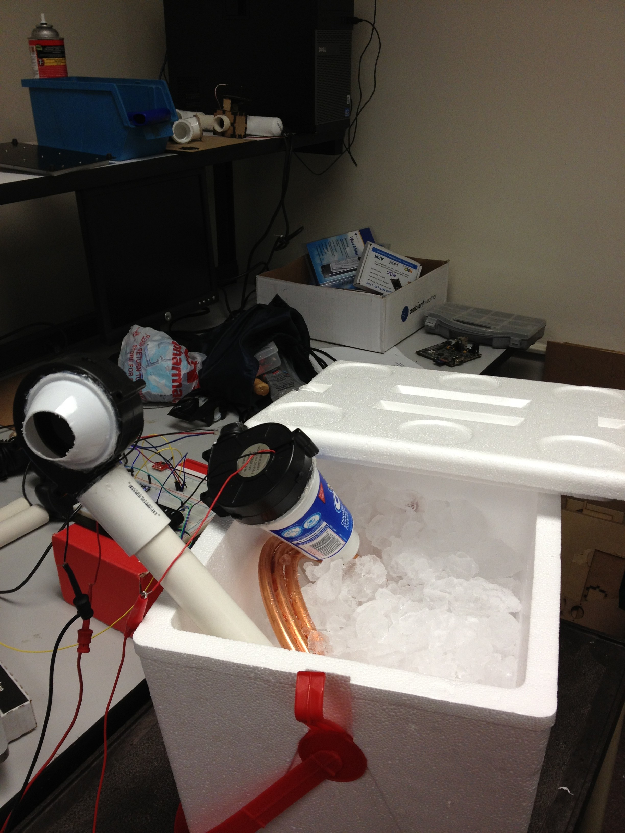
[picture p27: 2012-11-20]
PhotoShoot/Pics_11_11/Photo Nov 07, 2 32 55 PM.jpg

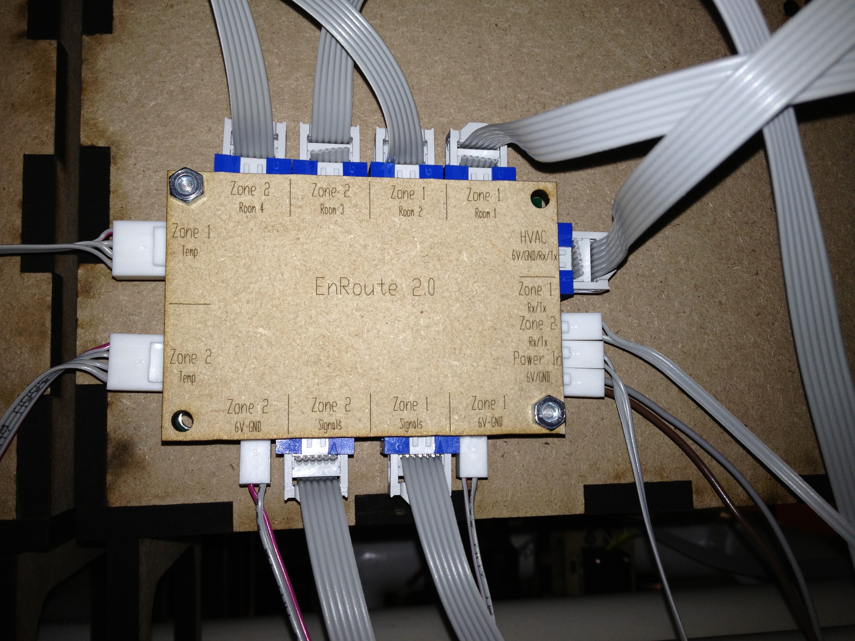
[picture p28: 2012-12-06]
PhotoShoot/Pics_11_30/Photo Nov 28, 2 20 52 PM.jpg

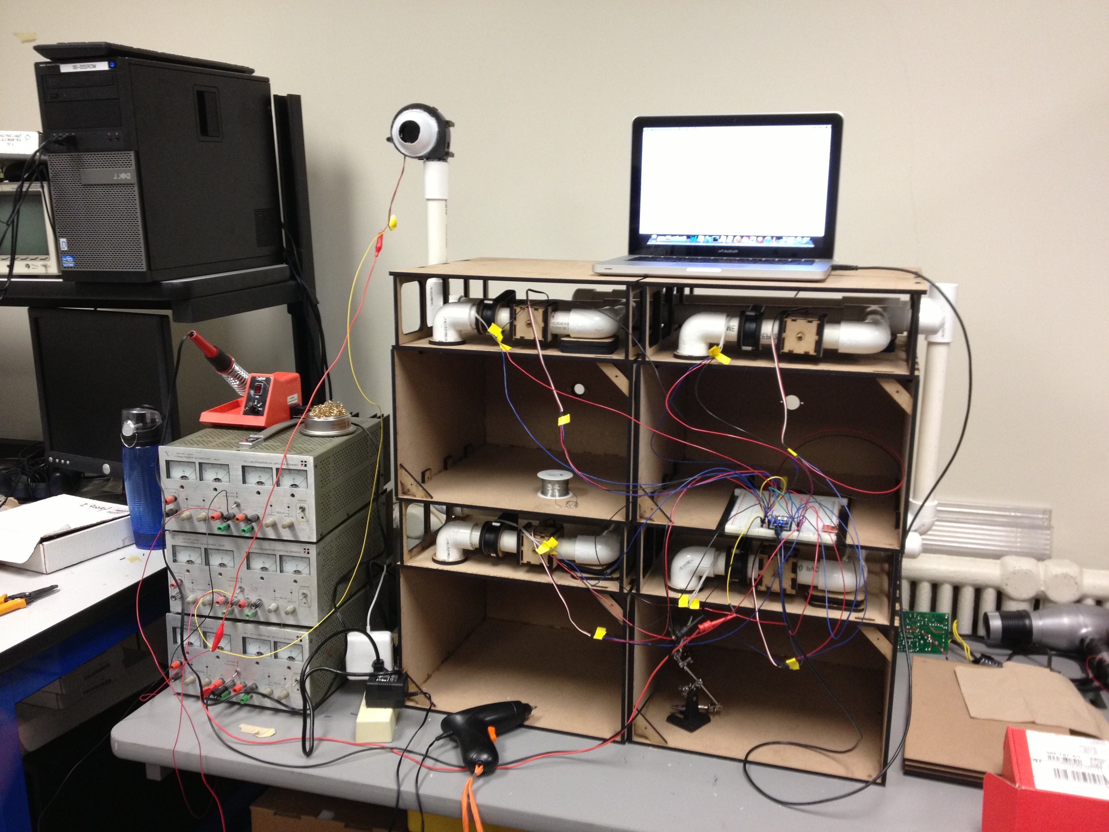
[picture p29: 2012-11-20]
PhotoShoot/Pics_11_11/Photo Nov 09, 5 29 56 PM.jpg

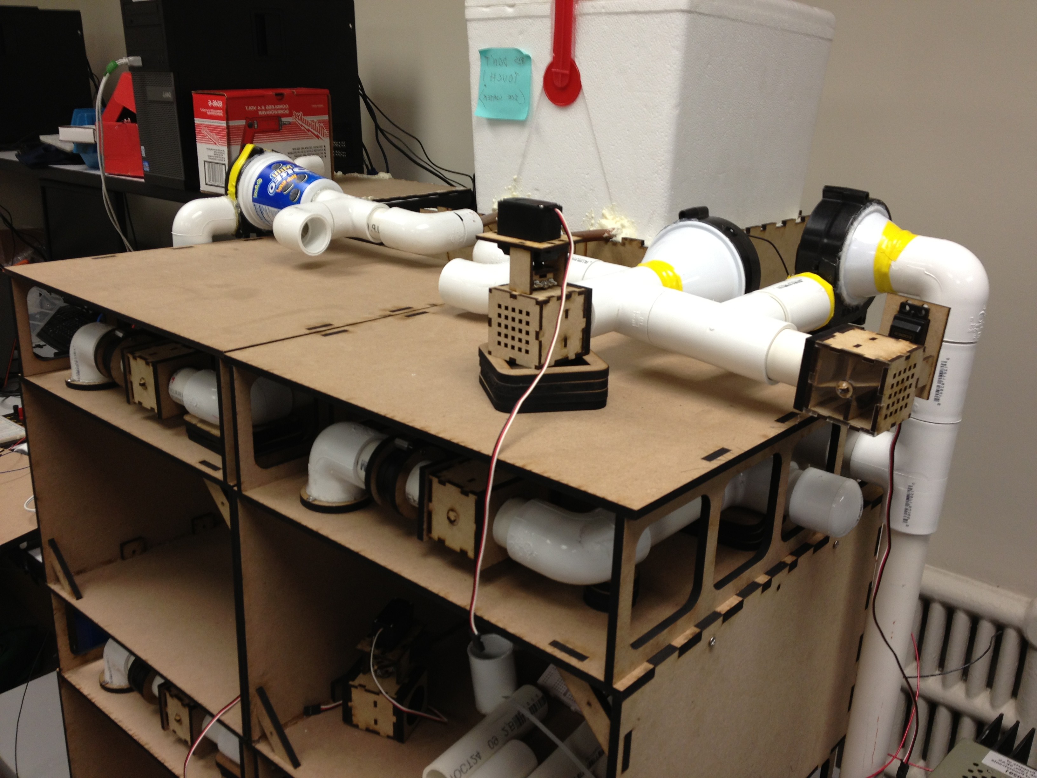
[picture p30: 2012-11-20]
PhotoShoot/Pics_11_19/Photo Nov 19, 3 16 20 PM.jpg

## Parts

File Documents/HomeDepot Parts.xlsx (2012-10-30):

Description | Price | Qty. | Total Price | Total
1" Sch. 40 PVC x 10 ft. | $3.33 | 2 | $6.66 | $65.84
1" tee | $0.86 | 6 | $5.16
1" elbow | $0.66 | 10 | $6.60
1" end cap | $0.66 | 2 | $1.32
PVC Cleaner | $7.21 | 1 | $7.21
PVC Cement | $6.97 | 1 | $6.97
10" Compact Hack Saw | $14.97 | 1 | $14.97
Spray Insulation | $4.28 | 1 | $4.28
U-Strap | $1.35
Silicone | ~$5.00
Insulation (2' x 8') | $12.67 | 1 | $12.67
Organization bag

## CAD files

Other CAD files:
CAD_EnRoute2.0/DoubleValveAssembly/DoubleValveAssembly.dwg
CAD_EnRoute2.0/ExhaustValveAssembly/ExhaustValveAssembly.dwg
CAD_EnRoute2.0/SingleValveAssembly/SingleValveAssembly.dwg
CAD_EnRoute2.0/Enclosure/MDF Framework/enclosure_front.dwg
CAD_EnRoute2.0/HVAC_Floor/HVAC_Floor.dwg
CAD_EnRoute2.0/HVAC_Floor/TopFloorToHVAC_Bridge/TopFloorToHVAC_Bridge.dwg
CAD_EnRoute2.0/Router_Cover/Router Cover.dwg
CAD_EnRoute2.0/SupportRings/inlet_outletSupportRing.dwg
CAD_EnRoute2.0/Valve Access - Standard/Cut_1.dwg
CAD_EnRoute2.0/Zone/RearWithWiringProvision.dwg
CAD_EnRoute2.0/Zone/CornerSupports.dwg
CAD_EnRoute2.0/Zone/LevelBridge_adjoiningWalls(2 per bridge).dwg
CAD_EnRoute2.0/Zone/AcrylicFrontCovers_Plain.dwg
CAD_EnRoute2.0/Zone/Original.dwg
CAD_EnRoute2.0/Enclosure/MDF Body_Walls/nut_LockMount.dwg

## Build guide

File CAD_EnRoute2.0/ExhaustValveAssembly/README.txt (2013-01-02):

Single Exhaust Valve:
The only main difference with the Exhaust Valve is the perforated wall that helps ease pressure in the unit. 
This piece can be seen in yellow.

EnRoute2.0

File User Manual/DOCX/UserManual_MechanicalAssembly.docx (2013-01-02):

EnRoute2.0 Assembling Instructions

The EnRoute2.0 assembly comprises of various materials including MDF (medium density fiber), PVC(PolyVinyl Chloride) pipes, Acrylic.

EnClosure:
Dimensions: 38.5” x 42.5” x 20”
Materials Used: 1/4” MDF and 1/4” Acrylic
Assembly: All the walls except the front of the enclosure were precisely cut using an electric saw due to dimensions exceeding our standard laser cutter bench,
The front of the enclosure is a combination of MDF framework and two 32”x16” clear acrylic sheets for ease of view of the HVAC testbed at work.

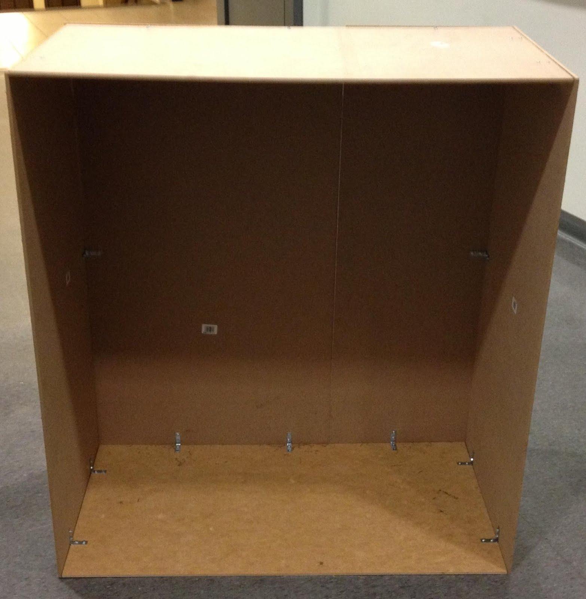
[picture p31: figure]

Fig 1 : Bare Enclosure

Room:
Dimensions: 14”x9”x14”
Materials Used: 1/4” MDF and 1/4” Acrylic
Assembly: The entire room was assembled from laser cut pieces, the CAD files for which can be found in our git repository. We also made small handles to easily remove the fronts when needed.

Fig 2 : 2 Zones 4 rooms

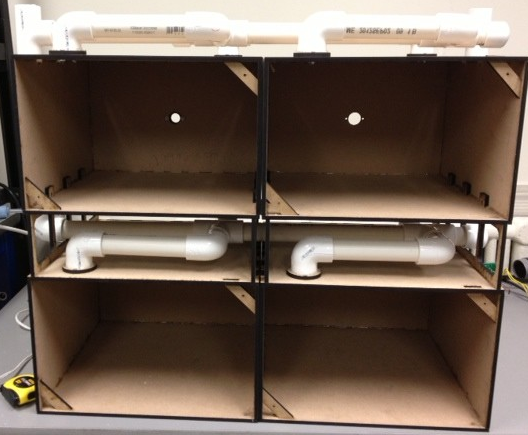
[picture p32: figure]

Valves:
Dimensions: Depending on what type of valve, the overall dimensions vary. However, the general stopping mechanism and the dimensions therein remain consistent in our system.
Materials Used: 1/4” MDF, 1/8” MDF, 1/8” clear Acrylic, plastic funnels.
Assembly: All the pieces except the shaft to the servo motor are press-fit. The Shaft assembly is a little tricky and contains a few very small pieces for a sturdy fit during rotation of the motor shaft. All these are available in the CAD files. We used funnels as a connector between the 1'' PVC pipe and the blower's inlet.

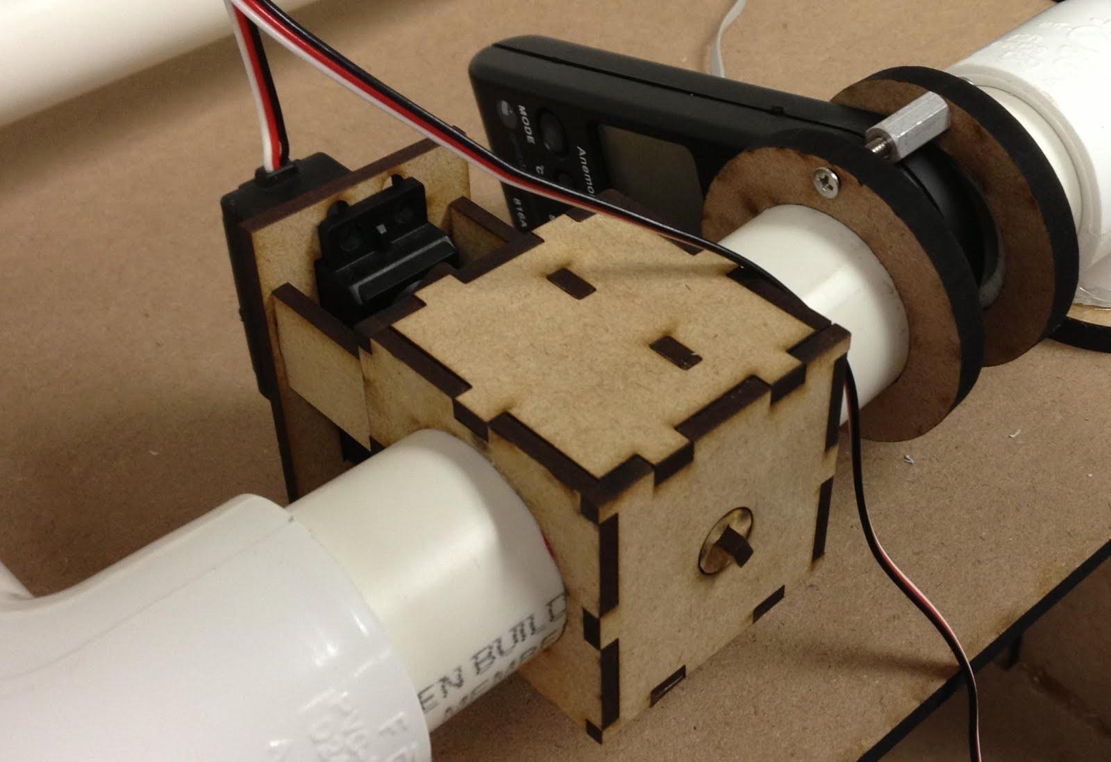
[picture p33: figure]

Fig 3 : Valve

Duct Work:
Dimensions / Material Used: 1” dia standard PVC pipe
We designed and placed all our components so as to have minimum ductwork for air to traverse.

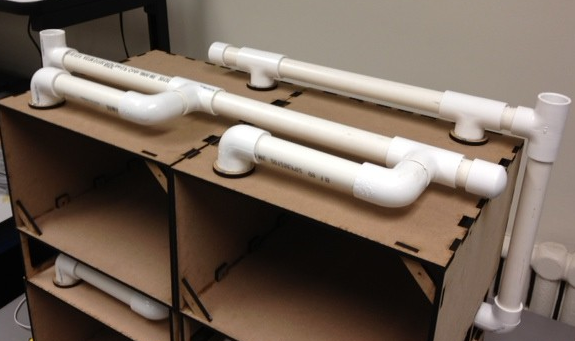
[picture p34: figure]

Fig 4 : Duct Work

Cooling:
Materials Used: Styrofoam box (13”x10”x11” ), Copper tubes (1” Dia, 2ft)
Assembly: The aforementioned copper was bent and the ends were used as inlet and outlet for the HVAC cooling system.

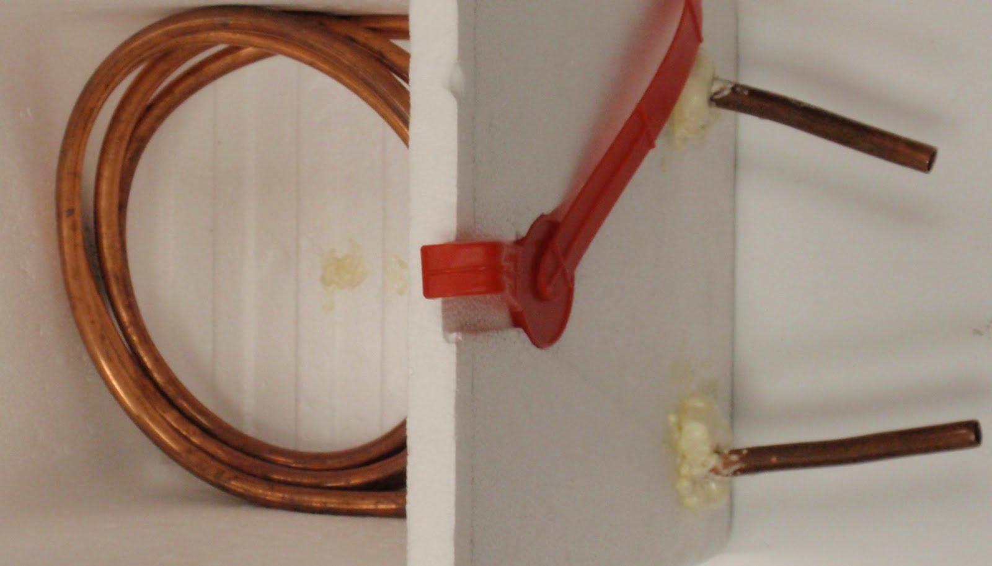
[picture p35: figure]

Fig 5 : Cooling box with Cu tubing

Heating:
Material Used: Hair dryer
Assembly: We used a funnel once again as a connector between one opening of the double valve and the inlet fan of the dryer. The outlet of the dryer was channeled to the main blower so as to heat the zones when required.

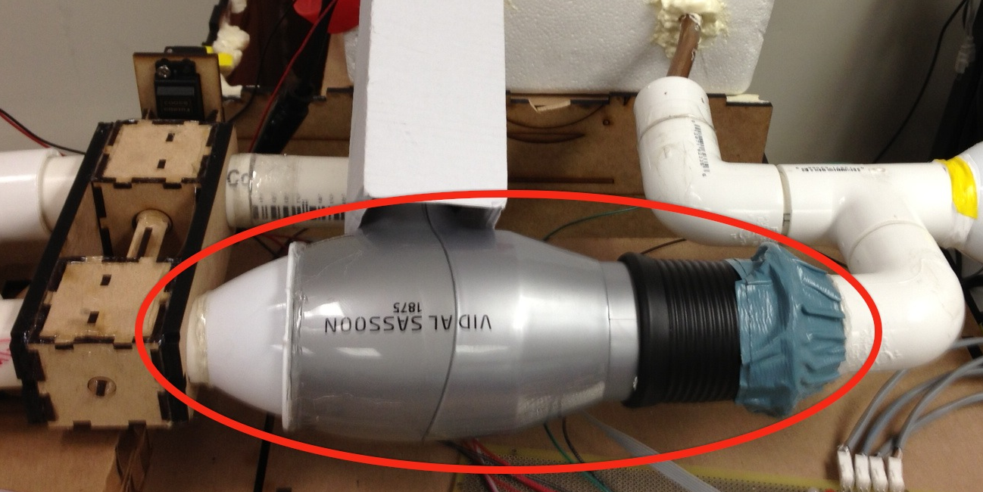
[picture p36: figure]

Fig 6 : Heating Mechanism with Double Valve

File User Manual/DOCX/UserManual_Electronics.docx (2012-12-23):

Electronics

EnRoute 2.0 uses a total of three (3) mbeds communicating over RS232 to read from sensors and control various actuators. The connections for each mbed are as follows:

HVAC mbed:

-Two (2) on-off blowers

-One (1) PWM-controlled blowers

-Two (2) servo valves

-One (1) flow meter

-Two (2) temperature sensors

-One (1) Ethernet port

-One (1) communication switch (IP v. Serial)

-One (1) on-off heater via dimmer switch

-Two (2) sets of RS232 communication lines from Zone1 and Zone2

-Five (5) status LEDs

Zone1 mbed:

-Two (2) servo valves

-Two (2) temperature sensors

-Two (2) flow meters

-One (1) set of RS232 communication lines

-One (1) 6V input signal for power and servos

Zone2 mbed:

-Two (2) servo valves

-Two (2) temperature sensors

-Two (2) flow meters

-One (1) set of RS232 communication lines

-One (1) 6V input signal for power and servos

To handle all the connections between the various mbeds there is a ‘Wiring Router’ located on the back of Room 1, as shown below in Figure 1. The energy router has a cover that labels what connections are supposed to be made and where, but the flow is given here as well.


Figure 1: Wiring Router

On the bottom of the right hand side there is an input for a 6 V supply, which is used to power Zone1 and Zone2 mbeds as well as provide power for all servo-motors. Directly above that are the input lines for Rx/Tx lines coming from Zone1 and Zone2. The remaining 6-pin connector on the right hand side is the output to the HVAC mbed, which includes two lines for 6 V, and four lines for the Rx/Tx lines from the other zones.

The top side includes four (4) 6-pin connectors, one for each room, which are for the servo valves (3 pins each) and flow meters (3 pins each).

The left side has two (2) 4-pin connections that go to rooms 2 and 4. These pins provide connections for temperature sensors (3.3V, GND, signal, vacant).

The bottom side has two (2) 2-pin connections that provide the 6 V signal to zones 1 and 2. Additionally there are two (2) 6-pin connectors that provide the two temperature sensor signals, two servo valve signals, and two flow meter signals to the zones for each mbed.

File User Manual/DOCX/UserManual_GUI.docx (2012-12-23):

GUI

The EnRoute 2.0 GUI has been written in MATLAB. It supports manual control of all functions as well as selecting Simulink defined control algorithms. Additionally, communication can be handled over the serial port or over IP so that the test-bed may be controlled remotely from any location. Here we will discuss how to use the GUI and any nuances that may be encountered.

Control Tab

The control tab, shown in Figure 1, is the first tab that should be considered before starting a simulation. This tab provides the following functions:

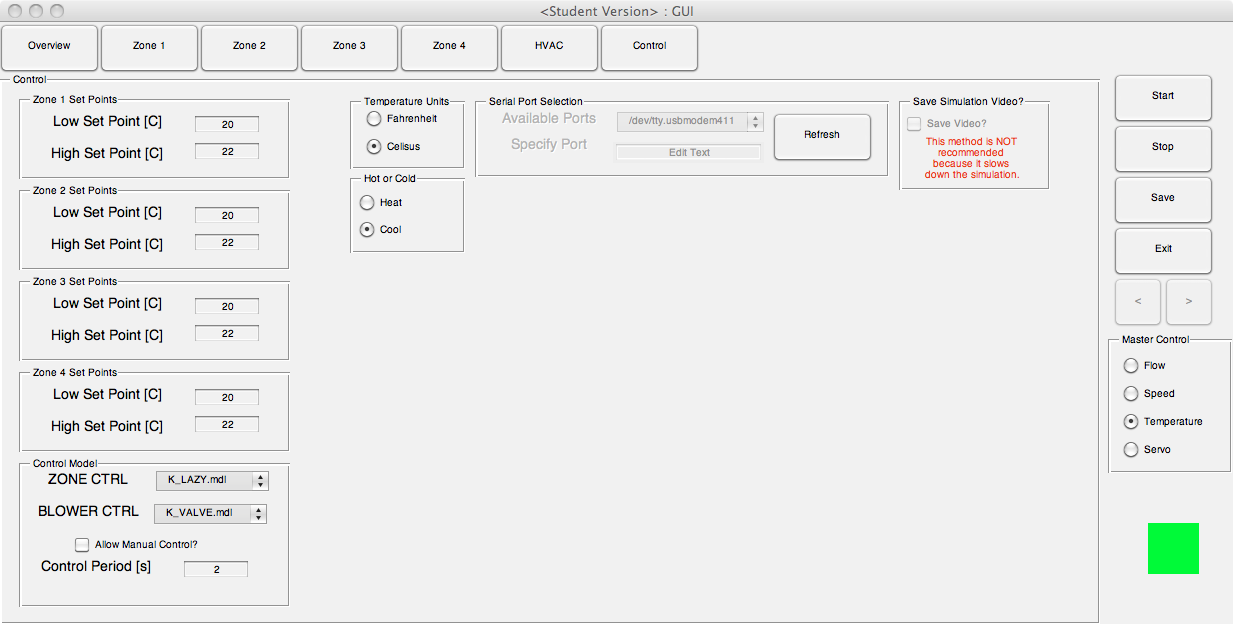
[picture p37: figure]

Figure 1: Control Tab

-Serial Port Selection

-IP Selection

-Save Video Option

-Temperature Unit Selection

-Heating or Cooling Selection

-Set Point Entry

-Control Model Selection

The Serial Port/IP selection box, shown in Figure 2, allows the user to choose between serial communication, IP communication, and allows for choosing the serial port of IP address for connecting. MATLAB should find any serial port that is connected to the computer, though this feature will only work on MAC or UNIX systems. This functionality can be seen in the SERIAL PORT/findPorts.m file. The ports will be updated when the program starts of the Control tab is selected, but you can manually update any time by pressing the refresh button. If your port is not listed, or you wish to set it manually, you can select the ‘Specify your own’ option and type the port name in the text field below the drop-down menu. As a final option, you can select ‘IP Communication’ and specify the IP address (the default address listed is correct unless any settings are changed on the IP side of things).

Figure 2: Serial Port/IP Selection Box

NOTE: There is a switch on the mbed circuit that toggles between IP or Serial communication. When the light is YELLOW it is set to Serial Communication, when the light is GREEN, IP Communication is selected. The mbed MUST be restarted after changing the state of this switch.

The Control Tab also allows you to set the high and low set points for each of the rooms separately, and choose the control method from the drop down list, shown in Figure 3. The ‘Allows Manual Control’ checkbox disables all control methods when selected, but allows the user to manually control all valves. The Control Period text box allows the user to enter how frequently the controlled states should be updated in the code.

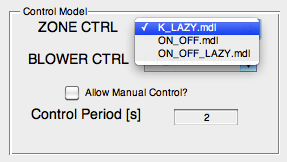
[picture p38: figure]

Figure 3: Control Model Selection

NOTE: The Control Period should NEVER be set to less than 1 second.

There are two drop-down menus, one will select the control algorithm used to specify the zone angles, and the selects the control algorithm for specifying blower speed based on the current valves or flow rates into the rooms. Designing new Simulink control models is discussed below.

The Temperature Units selection box allows you to change the displayed units to either Fahrenheit or Celsius.

NOTE: All temperature data stored in the output struct is in Celsius units.

The Save Video box allows you to specify whether or not you wish to save a video of your simulation. This will take screenshots of the GUI as you run a simulation and concatenate them all into a video.

NOTE: The video file will be rather large (hundreds of megabytes) for short simulations. It would be unrealistic to record a video for long simulations.

NOTE: When you start the simulation it will prompt for a video name; however, if you enter a name that already exists in the current directory the original file will be overwritten.

NOTE: The video recording will slow down the simulation.

NOTE: The output video will not be real time when played back.

The Heating/Cooling Selection box allows the user to specify whether the system is in heating or cooling mode. This checkbox will handle the double valve, and turn the heater on if needed. The heater has upper and lower bounds (37 C and 40 C) that are handled on the mbed to ensure it does not get hot enough to damage the system.

Overview Tab:

The Overview Tab, shown in Figure 4, allows the user to view all data from all the rooms on the same tab. The user can select individually what data to be plotted for each room using the radio button selection box to the right of each plot. Additionally, the data plotted in each graph can be synchronized using the master radio button selector all the way on the right of the GUI. Each plot has the current numerical value listed in the top left hand corner of the plot.

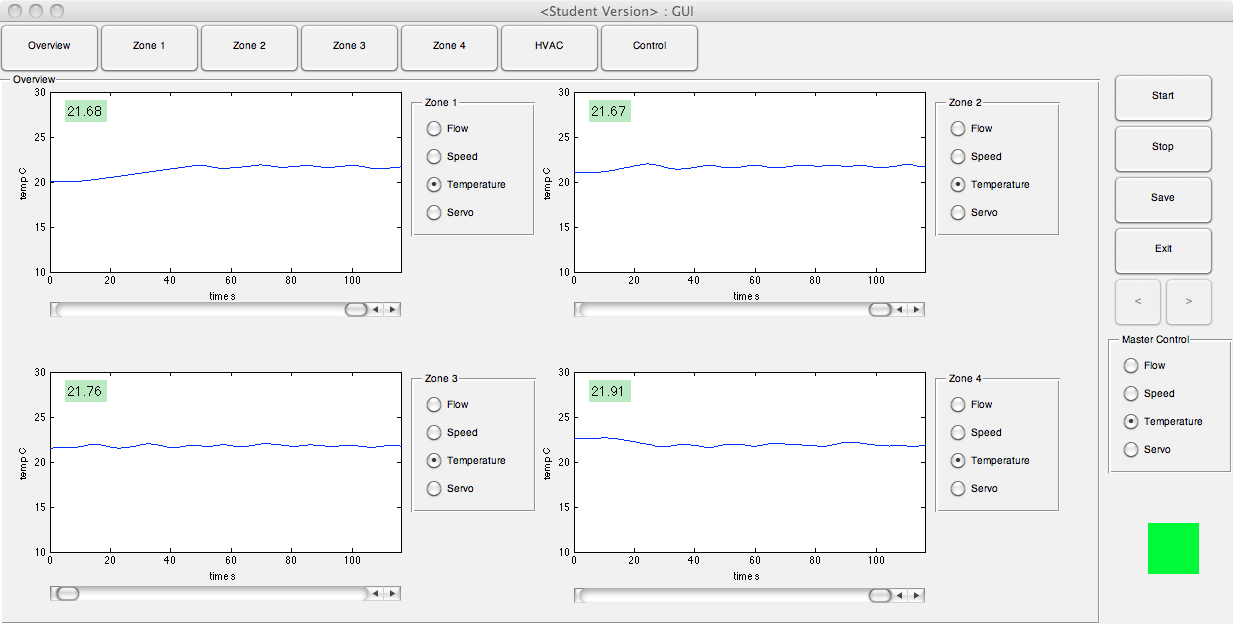
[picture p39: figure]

Figure 4: Overview Tab

The sliders allow for changing the servo position in each room

There are four (4) master control buttons on the right-hand side of the GUI: Start, Stop, Save, and Exit. Start will begin the simulation and Stop will end it. Exit will close the GUI. Save can be called after a simulation to save data to the current working directory. When you press the Save button you will be prompted to enter the name of the data to be saved and allows you to choose what should be saved from a series of check boxes. There is also a left and right arrow button, which allows you to scroll through the plotted data after the simulation is complete.

There are a variety of checks within the code that may present warnings after Start is pressed if the Serial Port is not specified correctly or working correctly.

NOTE: When you enter a Save As name MATLAB will check to see if any files with this title exist already, and will not allow you to overwrite any other files. However, this also means that you cannot save anything to the same name as other files, even if they have different extensions.

NOTE: It is highly recommended to press the Stop button before pressing the Exit button. Closing the GUI in any way either than the Exit button will cause errors to be displayed in MATLAB.

Zone Tabs:

The Zone Tab, shown in Figure 5, displays all the data for an individual zone. The radio button selector chooses which set of data is displayed in the large plot. All functionality is the same as the Overview Tab.

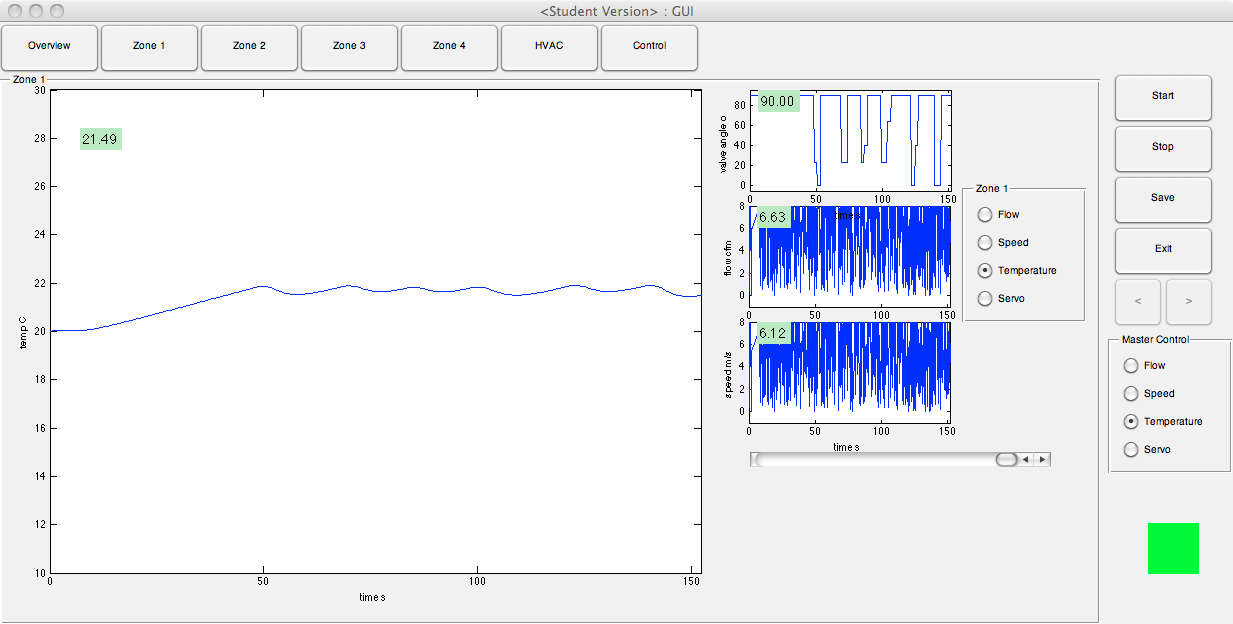
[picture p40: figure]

Figure 5: Zone Tab

HVAC Tab:

The HVAC tab, shown in Figure 6, controls all blowers, the recycle valves, and reads the temperature, flow, and power characteristics of the HVAC. The Return Air Blower and Cooler Blower are only ON-OFF controlled, but the Supply Blower has a variable control from 60%-100% of 12 V power applied to the blower (via an h-bridge). On the top left hand corner you can view the blower speed (60-100%), air flow, air speed, and HVAC outlet temperature. On the top right hand graph you can view the valve angle for the exhaust and recycle air valve. Selecting the valve from the menu on the right and moving the slider changes the valve position. Finally, the bottom right hand graph displays blower current, blower power, heater current, and heater power. At the moment, heater current and power are not measured.

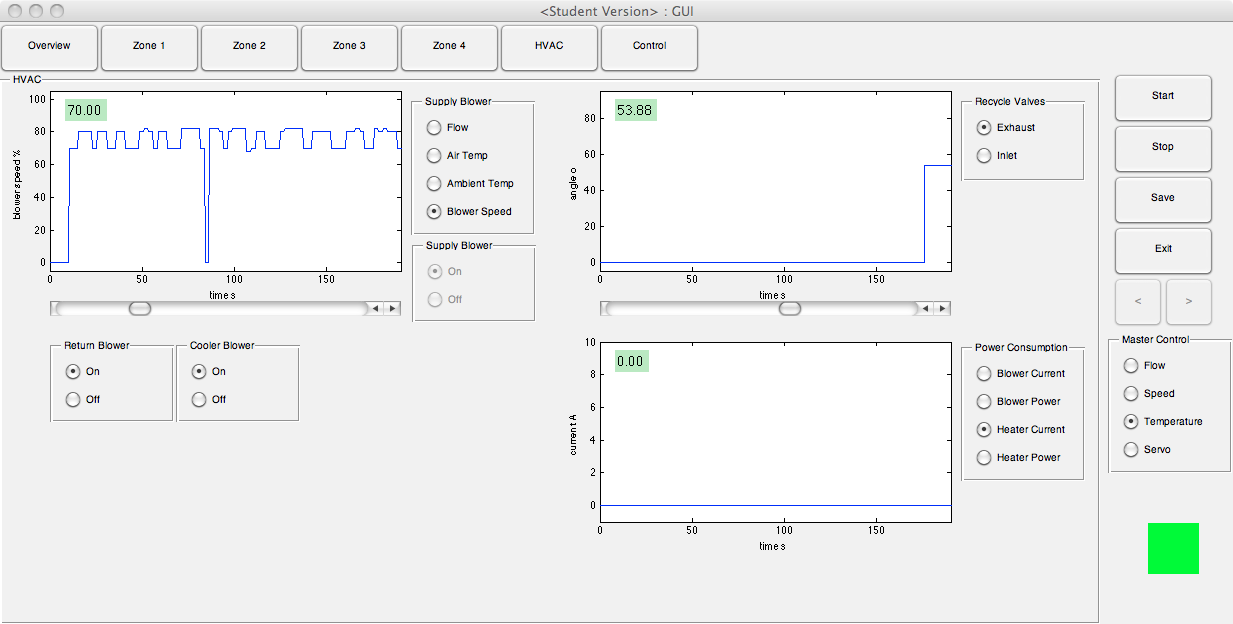
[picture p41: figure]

Figure 6: HVAC Tab

Control Models in Simulink

This GUI is designed so that users can define control structures in Simulink and run them directly from the GUI without any programming. The Simulink .mdl files must be placed in the correct folder (for blower control models place them in the CONTROL MODELS/HVAC folder, and for valve control models place them in the CONTROL MODELS/ZONE folder) for them to be found in the drop down menu.

If you wish to define a new model it is recommended you just save a copy of an existing model and rework it. Blower control models require eight (8) inputs (valve_1, valve_2, valve_3, valve_4, flow_1, flow_2, flow_3, flow_4) and one (1) output (blower state). Zone control models have eight (8) inputs (temp_1, temp_2, temp_3, temp_4, valve_1, valve_2, valve_3, valve_4) and four (4) outputs (valve_1, valve_2, valve_3, valve_4). If there are other inputs desired they can be manually entered using Constant blocks, or using Constant blocks and defining their states in the CONTROL MODELS/initControl.m file. Examples of this can be seen in the ON_OFF_LAZY.mdl file where additional inputs are applied with Constant blocks and the values for those constants are set in the initControl.m file.

Additionally, ON_OFF_LAZT.mdl shows how to code your own algorithm using a MATLAB function block in Simulink. This way, you can design your own controller without using standard Simulink blocks if you wish too.

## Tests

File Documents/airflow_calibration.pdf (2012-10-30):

y

=

0.0599x
R²

=

0.99838

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
Airflow

[m/s]

Pulse

Reading

[Hz]

# Airflow

# Calibra:on

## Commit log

2012-10-30 EnRoute Git Repo uploaded files
    [HomeDepot Parts.xlsx]
2012-11-02 Clean up
    [HomeDepot Parts.xlsx]
2012-11-02 Add DWG Files
    [Assemb.SLDASM, Assemb.dwg, Assemb_1.dwg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]
2012-12-15 deleted duplicate CAD file
    [Assemb.SLDASM, Assemb.dwg, Assemb_1.dwg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]
2013-01-02 CAD + UserManual Final Updates
    [AcrylicFrontCovers_Plain.dwg, Assemb.SLDASM, Assemb_1.dwg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]
